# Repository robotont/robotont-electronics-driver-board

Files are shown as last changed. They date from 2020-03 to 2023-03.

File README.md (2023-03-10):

# robotont-electronics-driver-board
The repository contains KiCAD schematics and PCB layout for the motor driver board.
The [production](Production/) folder contains prepared gerbers with pos file ready to order a from e.g. JLCPCB.

## Schematics
Schematic

## Layout

The following figures visualize the front and back side of the driver board along with the 3D model of the design.

Front side
Back side
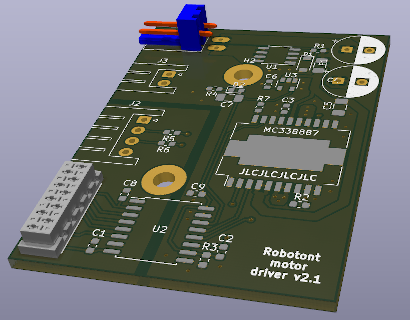
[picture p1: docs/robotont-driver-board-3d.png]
3D View


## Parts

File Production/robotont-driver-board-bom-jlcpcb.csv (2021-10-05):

Comment | Designator | Footprint | LCSC Part #
33nF | C3 | 0603 | C21117
10uF | C5,C7 | 1206 | C13585
100nF | C1,C2,C8,C9 | 0603 | C14663
MM1Z12 | D1 | SOD-123 | C115273
LED | D2 | 0603 | C72043
5A | F1 | 1206 | C182976
100k | R1 | 0603 | C25803
100 | R2 | 0603 | C22775
2k2 | R4 | 0603 | C4190
560 | R5,R6 | 0603 | C23204
10k | R7,R3 | 0603 | C25804
NTMS4807N | U1 | Package_SO:SO-8_3.9x4.9mm_P1.27mm | C80851
Si8641BD-B-IS | U2 | Package_SO:SOIC-16W_7.5x10.3mm_P1.27mm | C461891
MIC5205-X.X | U3 | Package_TO_SOT_SMD:SOT-23-5 | C70431

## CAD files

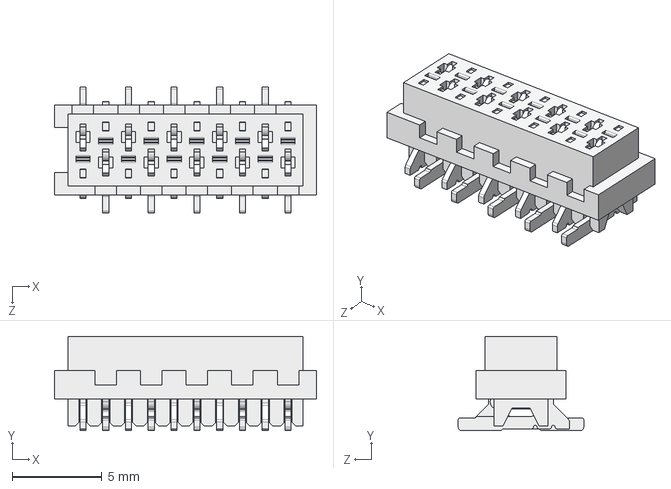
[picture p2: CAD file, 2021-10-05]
3d_models/MicroMaTch-10p-smd_p1-27_l14-6_w5_h5-25.step
14.6 x 5.25 x 7.00 mm

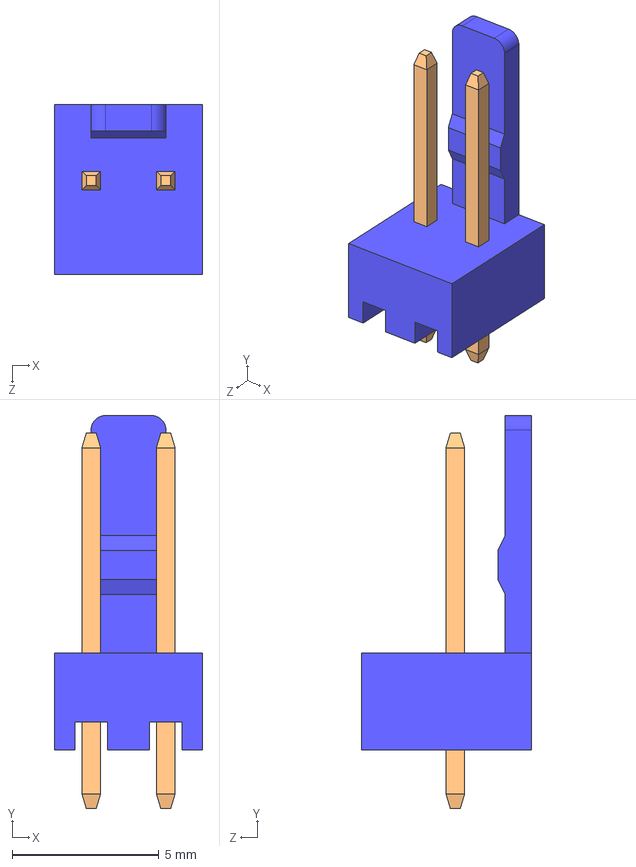
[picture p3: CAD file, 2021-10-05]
3d_models/2510-2pin_step.step
5.06 x 13.4 x 5.80 mm

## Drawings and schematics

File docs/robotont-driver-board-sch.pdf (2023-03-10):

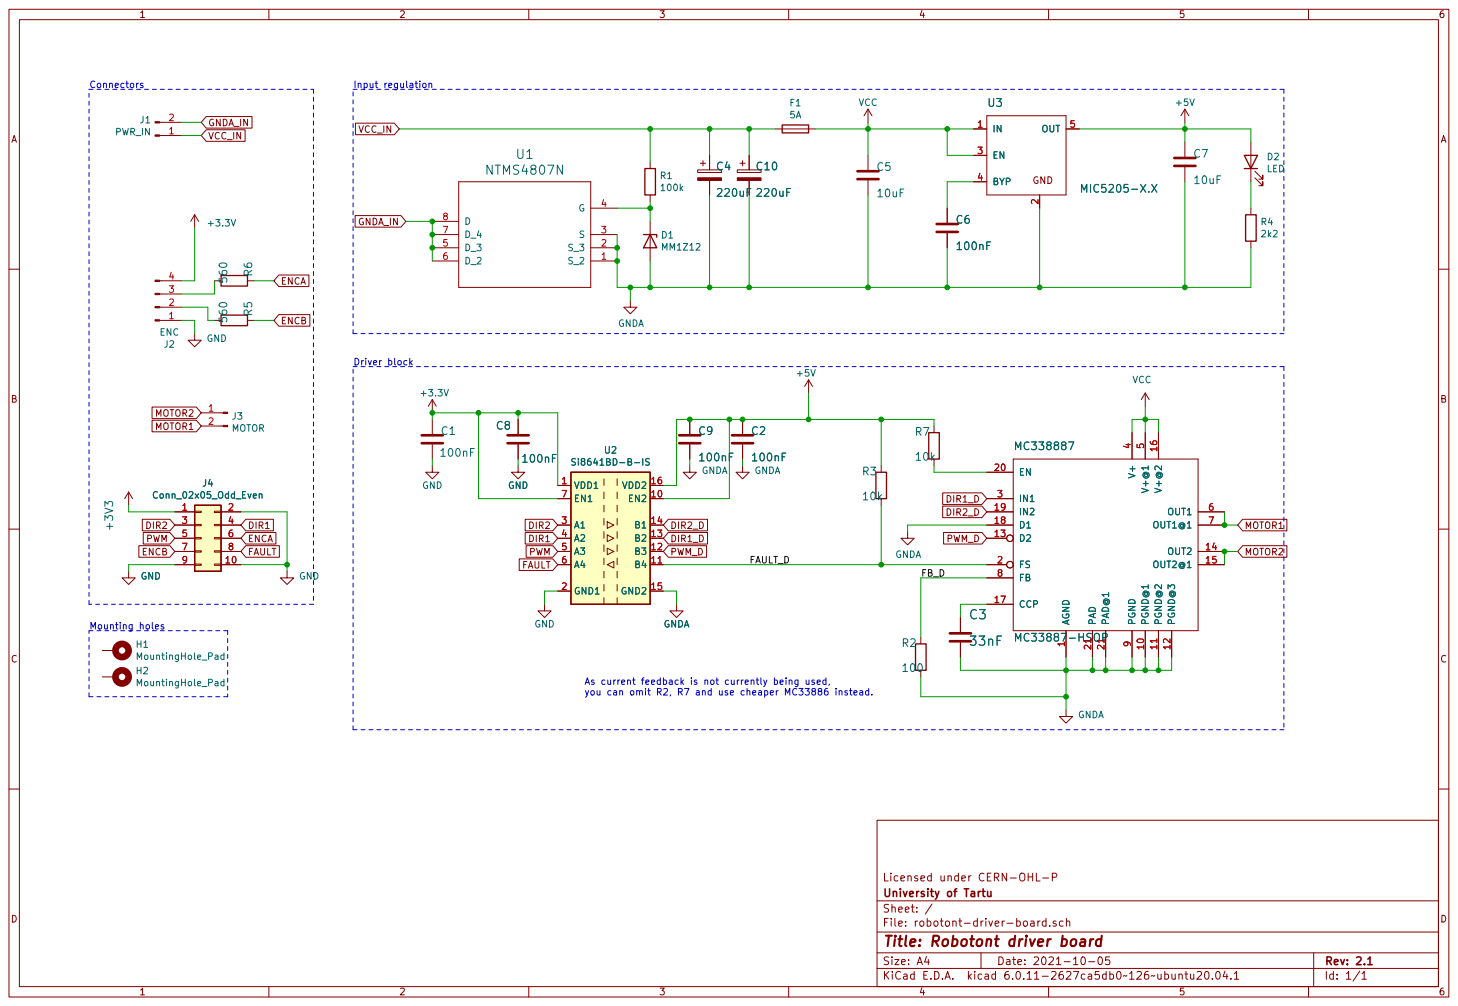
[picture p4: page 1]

Id: 1/1 Title: Robotont driver board

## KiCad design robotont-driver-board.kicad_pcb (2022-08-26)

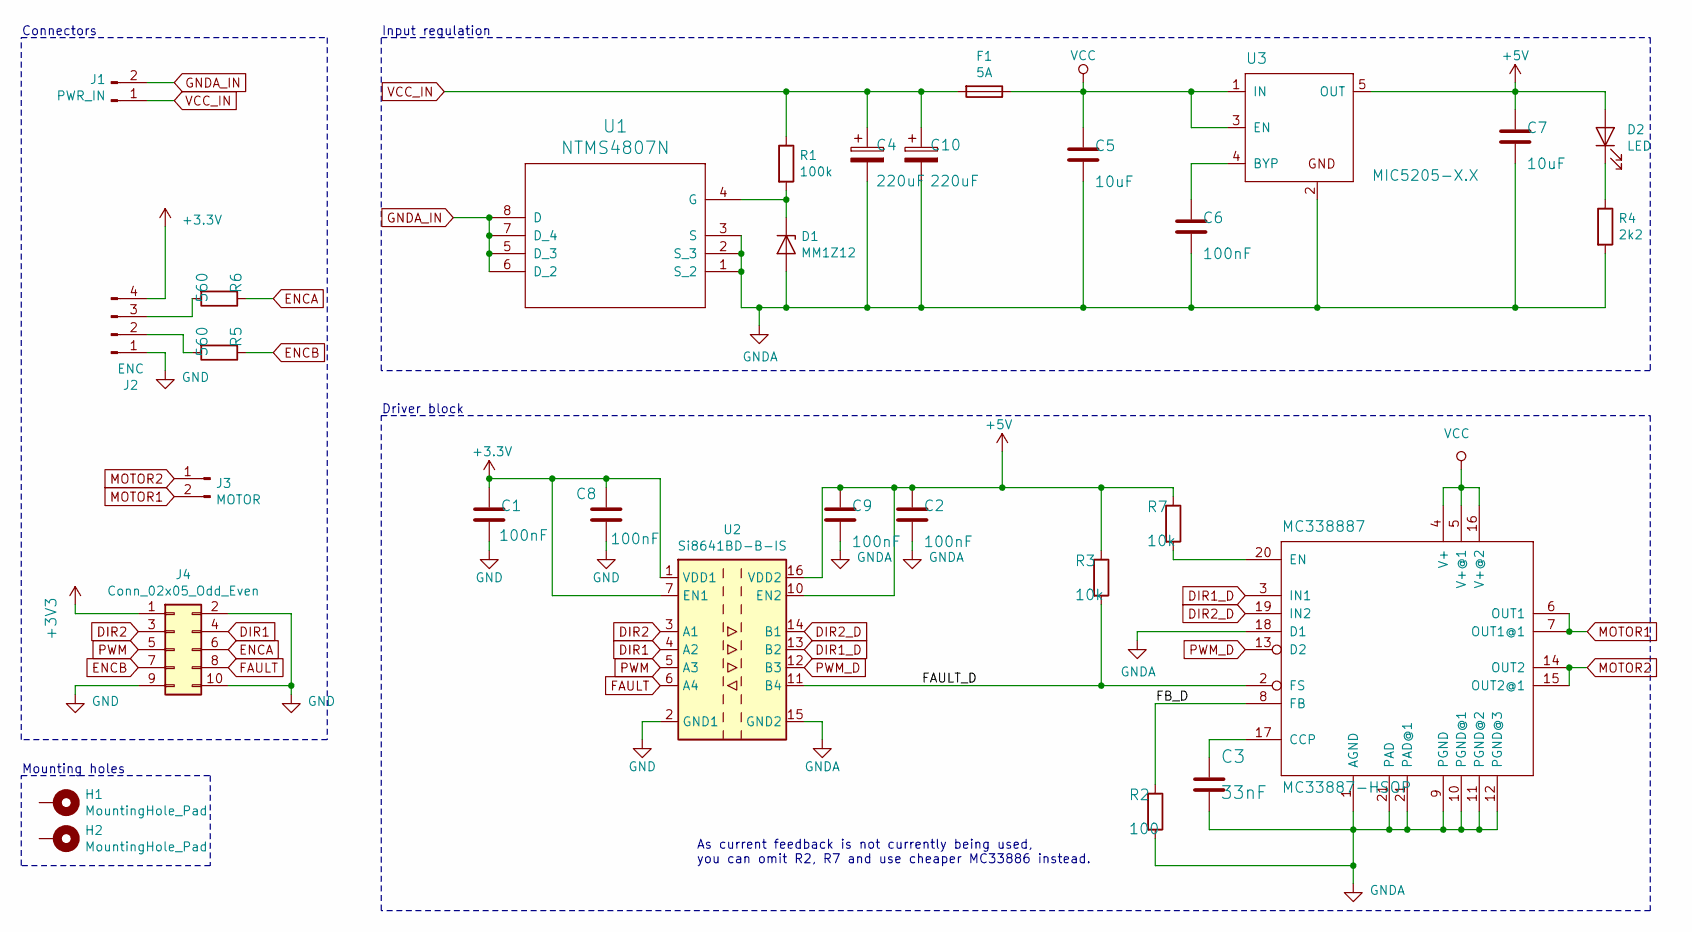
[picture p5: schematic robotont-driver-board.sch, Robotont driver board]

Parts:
C1, C2, C6, C8, C9: 100nF; C_0603_1608Metric; LCSC # C14663
C3: 33nF; C_0603_1608Metric; LCSC # C21117
C4, C10: 220uF; CP_Radial_D8.0mm_P3.50mm
C5, C7: 10uF; C_1206_3216Metric; LCSC # C13585
D1: MM1Z12; D_SOD-123; LCSC # C115273
D2: LED; LED_0603_1608Metric; LCSC # C72043
F1: 5A; Fuse_1206_3216Metric; LCSC # C182976
H1, H2: MountingHole_Pad; MountingHole_3mm_Pad
J1: PWR_IN; KF2510-2AWG
J2: ENC; JST_XH_S4B-XH-A_1x04_P2.50mm_Horizontal
J3: MOTOR; JST_XH_S2B-XH-A_1x02_P2.50mm_Horizontal
J4: Conn_02x05_Odd_Even; CONN-TE-MICROMATCH-5X2-PTH-BOSS
MC338887: MC33887-HSOP; HSOP-20-1EP_11.0x15.9mm_P1.27mm_SlugDown_ThermalVias
R1: 100k; R_0603_1608Metric; LCSC # C25803
R2: 100; R_0603_1608Metric; LCSC # C22775
R3, R7: 10k; R_0603_1608Metric; LCSC # C25804
R4: 2k2; R_0603_1608Metric; LCSC # C4190
R5, R6: 560; R_0603_1608Metric; LCSC # C23204
U1: NTMS4807N; SO-8_3.9x4.9mm_P1.27mm; LCSC # C80851
U2: Si8641BD-B-IS; SOIC-16W_7.5x10.3mm_P1.27mm; LCSC # C461891
U3: MIC5205-X.X; SOT-23-5; LCSC # C70431

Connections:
+5V: C2.1, C7.1, C9.1, D2.2 (A), R3.1, R7.1, U2.10 (EN2), U2.16 (VDD2), U3.5 (OUT)
/FAULT_D: MC338887.2 (FS), R3.2, U2.11 (B4)
/FB_D: MC338887.8 (FB), R2.1
DIR1: J4.4, U2.4 (A2)
DIR1_D: MC338887.3 (IN1), U2.13 (B2)
DIR2: J4.3, U2.3 (A1)
DIR2_D: MC338887.19 (IN2), U2.14 (B1)
ENCA: J4.6, R6.1
ENCB: J4.7, R5.1
FAULT: J4.8, U2.6 (A4)
GND: C1.2, C8.1, J2.1, J4.2, J4.9, J4.10, U2.2 (GND1), U2.8 (GND1)
GNDA: C2.2, C3.2, C4.2, C5.2, C6.2, C7.2, C9.2, C10.2, D1.2 (A), MC338887.1 (AGND), MC338887.9 (PGND), MC338887.10 (PGND@1), MC338887.11 (PGND@2), MC338887.12 (PGND@3), MC338887.18 (D1), MC338887.21 (PAD), R2.2, R4.2, U1.1 (S_2), U1.2 (S_3), U1.3 (S), U2.9 (GND2), U2.15 (GND2), U3.2 (GND)
GNDA_IN: J1.2, U1.5 (D_3), U1.6 (D_2), U1.7 (D_4), U1.8 (D)
MOTOR1: J3.2, MC338887.6 (OUT1), MC338887.7 (OUT1@1)
MOTOR2: J3.1, MC338887.14 (OUT2), MC338887.15 (OUT2@1)
unnamed: C3.1, MC338887.17 (CCP)
unnamed: C6.1, U3.4 (BYP)
unnamed: D1.1 (K), R1.2, U1.4 (G)
unnamed: D2.1 (K), R4.1
unnamed: J2.2, R5.2
unnamed: J2.3, R6.2
unnamed: MC338887.20 (EN), R7.2
PWM: J4.5, U2.5 (A3)
PWM_D: MC338887.13 (D2), U2.12 (B3)
VCC: C5.1, F1.1, MC338887.4 (V+), MC338887.5 (V+@1), MC338887.16 (V+@2), U3.1 (IN), U3.3 (EN)
VCC_IN: C4.1, C10.1, F1.2, J1.1, R1.1

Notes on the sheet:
Connectors
Mounting holes
Input regulation
Driver block
As current feedback is not currently being used, you can omit R2, R7 and use cheaper MC33886 instead.

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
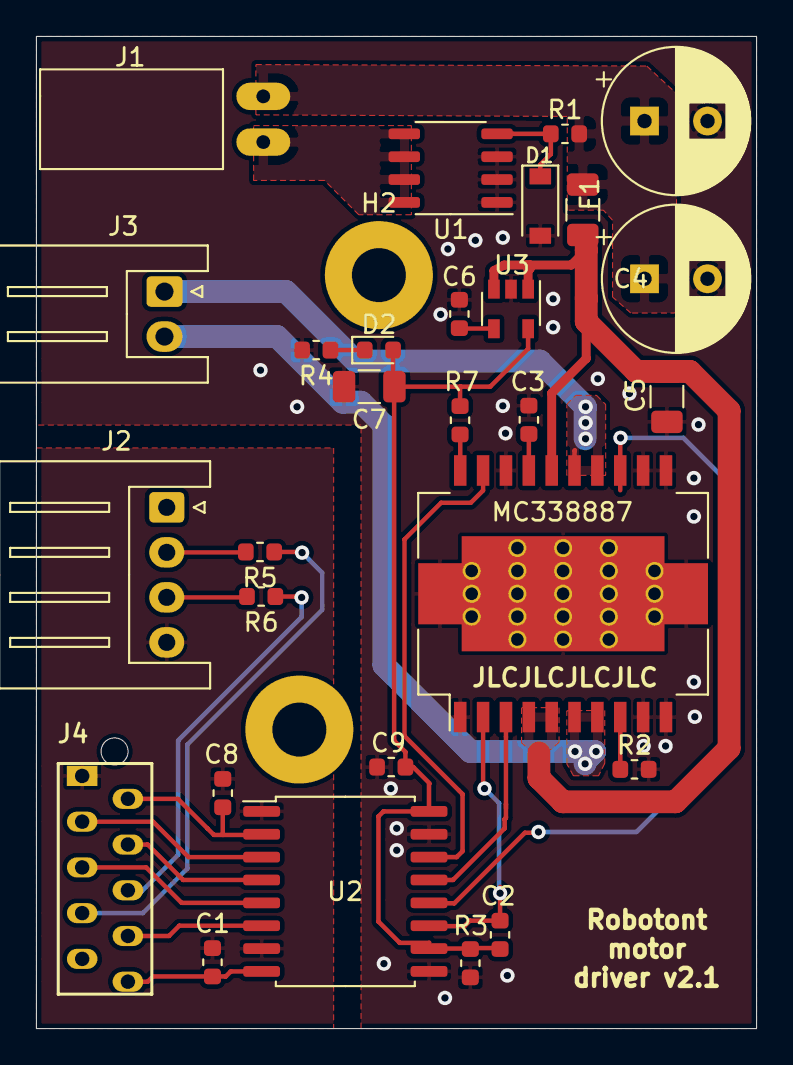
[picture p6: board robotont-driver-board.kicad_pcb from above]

Board: 2 copper layers, 40.0 x 55.1 mm, 30 parts (0 on the bottom side), 27 nets.

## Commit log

2020-03-27 schematic converted from eagle
    [robotont-motor-board.kicad_pcb, robotont-motor-board.sch]
2020-03-31 v2.1 with jlcpcb components
    [robotont-motor-board.kicad_pcb, robotont-motor-board.sch]
2021-10-05 some cleanup, CERN permissive license, included jlcpcb position files
    [2510-2pin_step.step, MicroMaTch-10p-smd_p1-27_l14-6_w5_h5-25.step, robotont-driver-board-bom-jlcpcb.csv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]
2022-08-26 added production files
    [robotont-driver-board-bom-jlcpcb.csv, robotont-driver-board.kicad_pcb, robotont-driver-board.sch]

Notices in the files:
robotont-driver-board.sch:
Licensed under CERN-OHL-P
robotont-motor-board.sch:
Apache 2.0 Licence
